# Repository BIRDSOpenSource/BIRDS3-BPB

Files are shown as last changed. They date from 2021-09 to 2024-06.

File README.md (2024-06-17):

<p align="center">
<a href="https://lean-sat.org/opensource/" class="button icon calendar">Join Monthly Webinar</a>
</p>

<div align="center">

</div>

# BIRDS3-BPB
The two different designs of the BPB used in the BIRDS3 mission, one with CPLD and one without.

## About the BIRDS3 Program:



The project was led by Kyushu Institute of Technology in Japan and involves students from Sri Lanka, Bhutan, Nepal and Japan.
Satellite Names: NepaliSat-1 (Nepal), Raavana-1 (Sri Lanka) and Ugiusu (Japan)

Stakeholders: Nepal Academy of Science and Technology (NAST) for Nepal, Arthur C Clarke Institute for Modern Technologies (ACCIMT) for Sri Lanka, and Kyushu Institute of Technology (Kyutech) for Japan.

Project duration: 2018-2020

CubeSat: 1U (10x10x10) cm3

Weight: 1.13kg

Launch Date: 17th April 2019

BIRDS-3 has 4 main missions in total; LoRa Demonstration Mission (LDM), Imaging Mission (CAM), Attitude Determination and Control Mission (ADCS) and Software Configurable Backplane Mission (BPB) 

## Organisation structure

## Features

## I like this project, can I help you?
You are welcome 🙂

* Give us a star ⭐
* Watch repository to be notified about updates 👀
* If you will find some errors, report them in Issues 🐞
* Try Birds designs on some real computer and let us know how it worked in Discussions. 💬
* We would greatly appreciate if you would also tell others about this ecosystem, it helps us to improve BIRDS Open Source. Thank you!

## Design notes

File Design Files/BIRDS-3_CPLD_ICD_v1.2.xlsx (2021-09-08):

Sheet: Version
BIRDS-3 BPB/CPLD Revision History
Date | Version | Person | Revision
22.05.18 | 1.0 | Abhas | Initial release of BPB/CPLD, updated with Turo

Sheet: Pin Assignment
 |  |  |  |  |  |  |  |  |  | `
C101 connector on the back plane |  | C102 connector on the back plane |  |  | C103 connector on the back plane |  | C104 connector on the back plane |  |  | C105 connector on the back plane |  |  | C106 connector on the back plane
FAB, Front access |  | EPS&OBC |  |  | COM |  | LDM |  |  | MSN II, Mission |  |  | RAB, Rear access
1 | Programming/debug 1 (DEV1 PGC) | 1 | Programming/debug 1 (DEV1 PGC) |  | 1 | COM_to_RAB GIO1 (DATA PROG PIN 1) | 1 | COM_to_RAB GIO1 (DATA PROG PIN 1) |  | 1 | COM_to_RAB GIO1 (DATA PROG PIN 1) |  | 1 | COM_to_RAB GIO1 (DATA PROG PIN 1)
2 | Programming/debug 2 (DEV 2 PGD) | 2 | Programming/debug 2 (DEV 2 PGD) |  | 2 | COM_to_RAB GIO2 (DATA PROG PIN 2) | 2 | COM_to_RAB GIO2 (DATA PROG PIN 2) |  | 2 | COM_to_RAB GIO2 (DATA PROG PIN 2) |  | 2 | COM_to_RAB GIO2 (DATA PROG PIN 2)
3 | Programming/debug 3 (DEV3 MCLR_FP) | 3 | Programming/debug 3 (DEV3 MCLR_FP) |  | 3 | COM_to_RAB GIO3 (DATA PROG PIN 3) | 3 | COM_to_RAB GIO3 (DATA PROG PIN 3) |  | 3 | COM_to_RAB GIO3 (DATA PROG PIN 3) |  | 3 | COM_to_RAB GIO3 (DATA PROG PIN 3)
4 | Programming/debug 4 (DEV4 MCLR_RP) | 4 | Programming/debug 4 (DEV4 MCLR_RP) |  | 4 | COM_to_RAB GIO4 (ADCS PROG PIN 1) | 4 | COM_to_RAB GIO4 (ADCS PROG PIN 1) |  | 4 | COM_to_RAB GIO4 (ADCS PROG PIN 1) |  | 4 | COM_to_RAB GIO4 (ADCS PROG PIN 1)
5 | Programming/debug 5 (DEV5 MCLR_CP) | 5 | Programming/debug 5 (DEV5 MCLR_CP) |  | 5 | COM_to_RAB GIO5 | 5 | COM_to_RAB GIO5 |  | 5 | MTQ_PWR_-X |  | 5 | MTQ_PWR_-X
6 | Programming/debug 6 (DEV6 MCLR_MP) | 6 | Programming/debug 6 (DEV6 MCLR_MP) |  | 6 | COM_to_RAB GIO6 | 6 | COM_to_RAB GIO6 |  | 6 | MTQ_RTN_-X |  | 6 | MTQ_RTN_-X
7 | FAB_to_RAB GIO 1 (ADCS PROG PIN 2) | 7 | OBC-COM 1 |  | 7 | OBC-COM 1 | 7 | FAB_to_RAB GIO 1 (ADCS PROG PIN 2) |  | 7 | FAB_to_RAB GIO 1 (ADCS PROG PIN 2) |  | 7 | FAB_to_RAB GIO 1 (ADCS PROG PIN 2)
8 | FAB_to_RAB GIO 2 (ADCS PROG PIN 3) | 8 | OBC-COM 2 |  | 8 | OBC-COM 2 | 8 | FAB_to_RAB GIO 2 (ADCS PROG PIN 3) |  | 8 | FAB_to_RAB GIO 2 (ADCS PROG PIN 3) |  | 8 | FAB_to_RAB GIO 2 (ADCS PROG PIN 3)
9 | FAB_to_RAB GIO 3(BC TEMP IN) | 9 | FAB_to_RAB GIO 3(BC TEMP IN) |  | 9 | FAB_to_RAB GIO 3(BC TEMP IN) | 9 | FAB_to_RAB GIO 3(BC TEMP IN) |  | 9 | FAB_to_RAB GIO 3(BC TEMP IN) |  | 9 | FAB_to_RAB GIO 3(BC TEMP IN)
10 | FAB_to_RAB GIO 4(MAIN_PIC_DIO to RAB BC) | 10 | FAB_to_RAB GIO 4(MAIN_PIC_DIO to RAB BC) |  | 10 | FAB_to_RAB GIO 4(MAIN_PIC_DIO to RAB BC) | 10 | FAB_to_RAB GIO 4(MAIN_PIC_DIO to RAB BC) |  | 10 | FAB_to_RAB GIO 4(MAIN_PIC_DIO to RAB BC) |  | 10 | FAB_to_RAB GIO 4(MAIN_PIC_DIO to RAB BC)
11 | FAB_to_RAB GIO 5(MAIN_PIC_DIO to ADCS) | 11 | FAB_to_RAB GIO 5(MAIN_PIC_DIO to ADCS) |  | 11 | FAB_to_RAB GIO 5(MAIN_PIC_DIO to ADCS) | 11 | FAB_to_RAB GIO 5(MAIN_PIC_DIO to ADCS) |  | 11 | FAB_to_RAB GIO 5(MAIN_PIC_DIO to ADCS) |  | 11 | FAB_to_RAB GIO 5(MAIN_PIC_DIO to ADCS)
12 | FAB_to_RAB GIO 6 (MAIN_PIC_DIO to CAM) | 12 | FAB_to_RAB GIO 6 (MAIN_PIC_DIO to CAM) |  | 12 | FAB_to_RAB GIO 6 (MAIN_PIC_DIO to CAM) | 12 | FAB_to_RAB GIO 6 (MAIN_PIC_DIO to CAM) |  | 12 | FAB_to_RAB GIO 6 (MAIN_PIC_DIO to CAM) |  | 12 | FAB_to_RAB GIO 6 (MAIN_PIC_DIO to CAM)
13 | GND_SYS | 13 | GND_SYS |  | 13 | GND_SYS | 13 | GND_SYS |  | 13 | GND_SYS |  | 13 | GND_SYS
14 | GND_SYS | 14 | GND_SYS |  | 14 | GND_SYS | 14 | GND_SYS |  | 14 | GND_SYS |  | 14 | GND_SYS
15 | SUP_5V0 | 15 | SUP_5V0 |  | 15 | SUP_5V0 | 15 | SUP_5V0 |  | 15 | SUP_5V0 |  | 15 | SUP_5V0
16 | SUP_5V0 | 16 | SUP_5V0 |  | 16 | SUP_5V0 | 16 | SUP_5V0 |  | 16 | SUP_5V0 |  | 16 | SUP_5V0
17 | FAB_to_OBC GIO 1 (MPIC_UART_TX_EXT) | 17 | FAB_to_OBC GIO 1 (MPIC_UART_TX_EXT) |  | 17 | CPLD-PIN 19 | 17 | CPLD-PIN 39 (MAIN_PIC_UART_TX to DATA) | INPUT TO MSN | 17 | MTQ_PWR_-Z |  | 17 | CPLD-PIN 65
18 | FAB_to_OBC GIO 2 (MPIC_UART_RX_EXT) | 18 | FAB_to_OBC GIO 2 (MPIC_UART_RX_EXT) |  | 18 | CPLD-PIN 20 | 18 | CPLD-PIN 40 (MAIN_PIC_UART_RX to DATA) | OUTPUT FROM MSN | 18 | MTQ_RTN_-Z |  | 18 | CPLD-PIN 66
19 | FAB_to_OBC GIO 3 (MPIC_FAB_UART_TX) | 19 | FAB_to_OBC GIO 3 (MPIC_FAB_UART_TX) |  | 19 | CPLD-PIN 21 | 19 | CPLD-PIN 41 (MAIN_PIC_DIO to DATA) | INPUT TO MSN | 19 | MTQ_PWR_-Y |  | 19 | CPLD-PIN 67
20 | FAB_to_OBC GIO 4 (MPIC_FAB_UART_RX) | 20 | FAB_to_OBC GIO 4 (MPIC_FAB_UART_RX) |  | 20 | CPLD-PIN 22 | 20 | CPLD-PIN 42 |  | 20 | MTQ_RTN_-Y |  | 20 | CPLD-PIN 68
21 | POWERSC_-Y | 21 | CPLD-PIN 8 (MAIN_PIC_UART_TX to DATA) | OUTPUT FROM OBC | 21 | CPLD-PIN 23 | 21 | CPLD-PIN 43 |  | 21 | CPLD-PIN XX (not decided) |  | 21 | CPLD-PIN 69
22 | TEMP_2 (-Y panel) | 22 | CPLD-PIN 9 (MAIN_PIC_UART_RX to DATA) | INPUT TO OBC | 22 | CPLD-PIN 24 | 22 | CPLD-PIN 44 |  | 22 | CPLD-PIN XX (not decided) |  | 22 | CPLD-PIN 70 |  | CN303 Battery Connector is not directly connected to Backplane, Connected to FAB
23 | SUP_UNREG_1 | 23 | SUP_UNREG_1 |  | 23 | SUP_UNREG_1 | 23 | SUP_UNREG_1 |  | 23 | SUP_UNREG_1 |  | 23 | SUP_UNREG_1
24 | SUP_UNREG_1 | 24 | SUP_UNREG_1 |  | 24 | SUP_UNREG_1 | 24 | SUP_UNREG_1 |  | 24 | SUP_UNREG_1 |  | 24 | SUP_UNREG_1
25 | SUP_3V3_2 | 25 | SUP_3V3_2 |  | 25 | SUP_3V3_2 | 25 | SUP_3V3_2 |  | 25 | SUP_3V3_2 |  | 25 | SUP_3V3_2 |  | Battery
26 | SUP_3V3_2 | 26 | SUP_3V3_2 |  | 26 | SUP_3V3_2 | 26 | SUP_3V3_2 |  | 26 | SUP_3V3_2 |  | 26 | SUP_3V3_2 |  | 1 | GND_ROOT
27 | POWERSC_+X | 27 | CPLD-PIN 10 (MAIN_PIC_UART_TX To CAM) | OUTPUT FROM OBC | 27 | CPLD-PIN 25 | 27 | CPLD-PIN 45 (MAIN_PIC_UART_TX To CAM) | INPUT TO MSN | 27 | CPLD-PIN 45 (MAIN_PIC_UART_TX To CAM) | INPUT TO MSN | 27 | CPLD-PIN 71 |  | 2 | GND_ROOT
28 | TEMP_1 (+X) | 28 | CPLD-PIN 11 (MAIN_PIC_UART_RX To CAM) | INPUT TO OBC | 28 | CPLD-PIN 26 | 28 | CPLD-PIN 46 (MAIN_PIC_UART_RX To CAM) | OUTPUT FROM MSN | 28 | CPLD-PIN 46 (MAIN_PIC_UART_RX To CAM) | OUTPUT FROM MSN | 28 | CPLD-PIN 72 |  | 3 | GND_ROOT
29 | RAW_POWER | 29 | RAW_POWER |  | 29 | CPLD-PIN 27 | 29 | CPLD-PIN 47 |  | 29 | CPLD-PIN 47 |  | 29 | CPLD-PIN 73 |  | 4 | GND_ROOT
30 | RAW_POWER | 30 | RAW_POWER |  | 30 | CPLD-PIN 28 | 30 | CPLD-PIN 48 |  | 30 | CPLD-PIN 48 |  | 30 | CPLD-PIN 74 |  | 5 | N.C.
31 | POWERSC_-X | 31 | CPLD-PIN 12 (FM2_SPI_CS) | INPUT TO OBC | 31 | CPLD-PIN 29 | 31 | CPLD-PIN 49 (FM2_SPI_CS) | OUTPUT FROM MSN | 31 | CPLD-PIN 49 (FM2_SPI_CS) | OUTPUT FROM MSN | 31 | CPLD-PIN 75 |  | 6 | PWR_BAT
32 | TEMP_5 (-X panel) | 32 | CPLD-PIN 13 (FM2_SPI_MOSI) | INPUT TO OBC | 32 | CPLD-PIN 30 | 32 | CPLD-PIN 50 (FM2_SPI_MOSI) | OUTPUT FROM MSN | 32 | CPLD-PIN 50 (FM2_SPI_MOSI) | OUTPUT FROM MSN | 32 | CPLD-PIN 76 |  | 7 | PWR_BAT
33 | POWERSC_-Z | 33 | CPLD-PIN 14 (FM2_SPI_MISO) | OUTPUT FROM OBC | 33 | CPLD-PIN 31 | 33 | CPLD-PIN 51 (FM2_SPI_MISO) | INPUT TO MSN | 33 | CPLD-PIN 51 (FM2_SPI_MISO) | INPUT TO MSN | 33 | CPLD-PIN 77 |  | 8 | PWR_BAT
34 | TEMP_3 (-Z panel) | 34 | CPLD-PIN 15 (FM2_SPI_SCK) | INPUT TO OBC | 34 | CPLD-PIN 32 | 34 | CPLD-PIN 52 (FM2_SPI_SCK) | OUTPUT FROM MSN | 34 | CPLD-PIN 52 (FM2_SPI_SCK) | OUTPUT FROM MSN | 34 | CPLD-PIN 78 |  | 9 | PWR_BAT
35 | SUP_UNREG_2 | 35 | SUP_UNREG_2 |  | 35 | SUP_UNREG_2 | 35 | SUP_UNREG_2 |  | 35 | SUP_UNREG_2 |  | 35 | SUP_UNREG_2 |  | 10 | HEATER_CNTRL_BAT
36 | SUP_UNREG_2 | 36 | SUP_UNREG_2 |  | 36 | SUP_UNREG_2 | 36 | SUP_UNREG_2 |  | 36 | SUP_UNREG_2 |  | 36 | SUP_UNREG_2 |  | 11 | TEMP_SENSOR_1
37 | POWERSC_+Y | 37 | CPLD-PIN 16 (MAIN_PIC_UART_TX To ADCS) | OUTPUT FROM OBC | 37 | CPLD-PIN 33 | 37 | CPLD-PIN 53 (CAM_UART_TX0) | OUTPUT FROM MSN | 37 | CPLD-PIN 53 (CAM_UART_TX0) | OUTPUT FROM MSN | 37 | CPLD-PIN 79 (CAM_UART_TX0) | INPUT TO RAB | 12 | TEMP_SENSOR_2
38 | TEMP_4 (+Y panel) | 38 | CPLD-PIN 17 (MAIN_PIC_UART_RX To ADCS) | INPUT TO OBC | 38 | CPLD-PIN 34 | 38 | CPLD-PIN 54 (CAM_UART_RX0) | INPUT TO MSN | 38 | CPLD-PIN 54 (CAM_UART_RX0) | INPUT TO MSN | 38 | CPLD-PIN 80 (CAM_UART_RX0) | OUTPUT FROM RAB
39 | Kill SW | 39 | Kill SW |  | 39 | CPLD-PIN 35 | 39 | CPLD-PIN 55 (CAM_DTR) | INPUT TO MSN | 39 | CPLD-PIN 55 (CAM_DTR) | INPUT TO MSN | 39 | CPLD-PIN 81 (CAM_DTR) | OUTPUT FROM RAB
40 | DEP_SW-1 | 40 | DEP_SW-1 |  | 40 | CPLD-PIN 36 | 40 | CPLD-PIN 56 |  | 40 | CPLD-PIN 56 |  | 40 | CPLD-PIN 82
41 | DEP_SW-2 | 41 | DEP_SW-2 |  | 41 | CPLD-PIN 37 | 41 | CPLD-PIN 57 |  | 41 | CPLD-PIN 57 |  | 41 | CPLD-PIN 83
42 | CPLD-PIN 1 / DEP_SW-3 | 42 | CPLD-PIN 18 (MAIN_PIC_DIO to Data) | OUTPUT FROM OBC | 42 | CPLD-PIN 38 | 42 | CPLD-PIN 58 |  | 42 | CPLD-PIN 58 |  | 42 | CPLD-PIN 84
43 | CPLD-PIN 2 / DEP_SW-4 | 43 | OBC-COM 3 |  | 43 | OBC-COM 3 | 43 | CPLD-PIN 59 (MAIN_PIC_UART_TX To ADCS) | INPUT TO MSN | 43 | CPLD-PIN 59 (MAIN_PIC_UART_TX To ADCS) | INPUT TO MSN | 43 | CPLD-PIN 85
44 | CPLD-PIN 3 / TEMP_6 | 44 | OBC-COM 4 |  | 44 | OBC-COM 4 | 44 | CPLD-PIN 60 (MAIN_PIC_UART_RX To ADCS) | OUTPUT FROM MSN | 44 | CPLD-PIN 60 (MAIN_PIC_UART_RX To ADCS) | OUTPUT FROM MSN | 44 | CPLD-PIN 86
45 | CPLD-PIN 4 | 45 | OBC-COM 5 |  | 45 | OBC-COM 5 | 45 | CPLD-PIN 61 |  | 45 | CPLD-PIN 61 |  | 45 | CPLD-PIN 87
46 | CPLD-PIN 5 | 46 | OBC-COM 6 |  | 46 | OBC-COM 6 | 46 | CPLD-PIN 62 |  | 46 | CPLD-PIN 62 |  | 46 | CPLD-PIN 88
47 | CPLD-PIN 6 | 47 | OBC-COM 7 |  | 47 | OBC-COM 7 | 47 | CPLD-PIN 63 |  | 47 | CPLD-PIN 63 |  | 47 | CPLD-PIN 89
48 | CPLD-PIN 7 | 48 | OBC-COM 8 |  | 48 | OBC-COM 8 | 48 | CPLD-PIN 64 |  | 48 | CPLD-PIN 64 |  | 48 | CPLD-PIN 90
49 | SUP_3V3_1 | 49 | SUP_3V3_1 |  | 49 | SUP_3V3_1 | 49 | SUP_3V3_1 |  | 49 | SUP_3V3_1 |  | 49 | SUP_3V3_1
50 | SUP_3V3_1 | 50 | SUP_3V3_1 |  | 50 | SUP_3V3_1 | 50 | SUP_3V3_1 |  | 50 | SUP_3V3_1 |  | 50 | SUP_3V3_1
*Same colours and names are representing the same connection

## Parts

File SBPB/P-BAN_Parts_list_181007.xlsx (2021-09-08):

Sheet: 必ずお読みください
入力項目説明
メ ー カ ー |  |  | 電子部品のメーカー名をご入力ください。
部 品 種 別 |  |  | 電子部品の種別をご入力ください。例：チップ抵抗、トランジスタ、LED、など
電 子 部 品 型 番 |  |  | 電子部品の型番をご入力ください。 ※誤表記による不具合を回避するためにも正確なご入力をお願い致します。 ※表面実装の抵抗やコンデンサ(電解、タンタル以外)は、後述「電子部品見取り表」をご参照のうえ、ご入力ください。
配 置 記 号 / リファレンス |  |  | シルク図/配置図に表記された配置記号/リファレンス番号をご入力ください。 ※複数入力する場合は、カンマ「,」区切りでのご入力をお願い致します。 ※電子部品型番ベースでのご記入をお願い致します。（１つの電子部品型番に対して、配置番号を複数記入）
個 数 |  |  | 電子部品の個数をご入力ください。
ピ ン 数 |  |  | 電子部品の総ピン数をご入力ください。 ※基板取付穴、部品取付穴、全てのスルー・ノンスルーホール、面実装部品のパッド、及び次の①～⑤の配線を伴う箇所（①テストピン、②チェックランド、③引き出しランド、④ジャンパピン、⑤入出力ランドの総計。
実装 / 未実装 |  |  | 実装サービスでの「実装」/「未実装」をご選択ください。 ※同じ電子部品型番の中で実装と未実装が分かれる場合は、それぞれ2行に分けて配置記号をご入力ください。
部品分類 | SMD |  | 表面実装部品
 | DIP |  | 挿入部品
 | 特殊 BGA等 |  | BGA/CSP/LGA/QFNなど部品極性が部品の真下に配置された部品 -BGA：Ball Grid Array/下面に半田ボールの端子を配置したパッケージ。 -CSP：Chip Size Package/チッププサイズと同じか、もしくは僅かに大きいパッケージ。 -LGA：Land Grid Array/裏面に外部入出力用のランドを設けたパッケージ。※BGAの半田ボールがない。 -QFN：Quad Flat Non-Lead Package/QFPに似ていますが、外部入出力用のピンが出ていないパッケージ。
P板.com提供部品 (無料) |  |  | 【無償提供部品一覧】シートに記載されている「メーカー型番」を【部品リスト入力フォーム】シートのD列（電子部品型番）に入力し、I列（実装／未実装）を「実装」に設定いただくと、自動的に「○」が表示されます。 ※無料提供部品：チップコンデンサ/チップ抵抗を約1000種、実装サービスをご利用のお客様に無料提供いたします。 ※「○」が付かない場合は全半角の不一致などにより誤判定されている可能性があります。【無償提供部品一覧】シートより型番をコピー＆ペーストにて【部品リスト入力フォーム】にご入力ください。
 |  |  | http://www.p-ban.com/implementation/chip.html
P板.com調達部品(有料） |  |  | P板.com実装サービスで部品調達を希望される場合に○をご選択ください。 ※調達費用のお見積もりは、部品リストの返却と同時にご連絡いたします。 ※ご希望の納期や市場在庫状況によっては、調達が不可となる部品もございますので、予めご了承ください。
パッケージ情報 部品外形/部品仕様 |  |  | 電子部品のパッケージ情報をご入力ください。例：1608 , DIP , 0.5mmピッチQFP , 0.4mmピッチCN
コ メ ン ト |  |  | 特別なご指示のある電子部品について、自由にご入力ください。 例：未実装挿入穴のマスク処理が必要、など
版、変更履歴 |  |  | 部品種毎に、変更履歴を記載してください。 版は、アカウント登録の版に合わせて記載ください。
調達型式、代替型式 |  |  | 無料提供部品の在庫切れや、正確な調達型式を記載いたします。
部品名称見取り表
1.チップ部品（抵抗、コンデンサ）
 |  |  |  |  | 単位：ｍｍ
 |  |  | 電子部品型番 (C:コンデンサ、R:抵抗） | Ａ寸法 | Ｂ寸法
 |  |  | C/R1608 | 1.6 | 0.8
 |  |  | C/R2125 | 2 | 1.25
 |  |  | C/R3216 | 3.2 | 1.6
 |  |  | C/R3225 | 3.2 | 2.5
 |  |  | C/R4532 | 4.5 | 3.2
2.チップタンタルコンデンサ
 |  |  |  |  | 単位：ｍｍ
 |  |  | 電子部品型番 | Ａ寸法 | Ｂ寸法
 |  |  | CT3216 | 3.2 | 1.6
 |  |  | CT3528 | 3.5 | 2.8
 |  |  | CT4726 | 4.7 | 2.6
 |  |  | CT6032 | 6 | 3.2
 |  |  | CT5846 | 5.8 | 4.6
 |  |  | CT7343 | 7.3 | 4.3
3.チップアルミ電解コンデンサ
 |  |  |  |  |  | 単位：ｍｍ
 |  |  | 電子部品型番 | Ａ寸法 | Ｂ寸法 | C寸法
 |  |  | CE33 | 3.3 | 3.3 | φ3.0
 |  |  | CE43 | 4.3 | 4.3 | φ4.0
 |  |  | CE53 | 5.3 | 5.3 | φ5.0
 |  |  | CE66 | 6.6 | 6.6 | φ6.3
 |  |  | CE83 | 8.3 | 8.3 | φ8.0
 |  |  | CE103 | 10.3 | 10.3 | φ10.0
部品取り付け穴は、ピン数に含めてください。
コネクタの場合 |  |  |  |  |  | トランスの場合
部品リストフォーマット変更履歴
2014-02-01 | v2.0 | 松森 | 部品種別の総計を、直接関数に変更
 |  |  | ピン数合計、実装数合計数量を、直接関数に変更
 |  |  | 部品調達見積欄を修正
2014-03-11 | v2.1 | 松森 | *N列、O列が下の方、"○"選択リスト消えていたのを追加
 |  |  | *縮小しても解像度崩れず文字表示するため、フォントを"Meiryo UI"(Windows 標準添付)に変更
 |  |  | *136行目以降を非表示
 |  |  | *"X"列にリストを埋め込み
2014-06-12 | v2.2 | 松森 | *固定行を変更
 |  |  | *在庫状況列に条件付き書式設定
 |  |  | *その他各種バグ修正
2015-03-31 | V2.3 | 松森 | *無償提供部品を記載すると、無償提供部品欄に自動で"○"が表示されるよう条件式を挿入
 |  |  | *併せて、無償提供部品参照用一覧シートの作成・追加
 |  |  | *最小購入数が必要数量を下回る場合、セルを赤色にハッチングする
 |  |  | *シート1の名称変更
 |  |  | *変更履歴シートの追加
2015-06-19 | v2.4 | 松森 | ・ゼロΩ抵抗を無償対象に追加
 |  |  | ・変更履歴の列を追加し、変更履歴シートを削除
 |  |  | ・その他書式、印刷機能の変更
 |  |  | ・無償提供部品の入れ替え
2015-08-14 | v2.5 | 松森 | ・ゼロΩ抵抗の無償対象品が正しく反映されていなかったバグ修正
 |  |  | ・フォームへバージョン情報を埋め込み
2015-11-05 | v2.6 | 上田 | ・無償提供部品(RK73H2ATTD1601F)の抵抗値を正しい値に修正
2015-11-09 | v2.7 | 上田 | ・P板.com調達部品(無料)欄のフォントを変更
2016-01-15 | v2.8 | 箕浦 | ・無償提供部品一覧の「GRM32NF11E106Z」を削除
 |  |  | ・部品リスト入力フォームの4行目F列～L列の計算式が136行目以降を対象としていなかった不具合を修正
2016-01-27 | v2.9 | 箕浦 | ・「無償提供部品一覧」シートの表記修正

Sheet: 部品リスト入力フォーム
Ver.8.0 |  |  | 電 子 部 品 型 番 ※半角英数字 ※サフィックスまで入力必須 | 配 置 記 号 リ フ ァ レ ン ス ※半角英数字） | 個数 | ピ ン 数 (部品取付穴 を含む） |  | 実装/ 未実装 | 部 品 分 類 |  |  | 必要数 実装枚数を入れてください。 ↓ | P板.com 提供 部品 (無料) | P板.com 調達 部品 (有料） | パッケージ情報 部品外形/部品仕様 | コ メ ン ト ※未実装挿入穴の マスク処理が必要、など | 版 変更履歴 | 入荷数 | 返却
No | メーカー | 部品種別 |  |  |  | 1個 あたり | 合計 | 実装個数 | SMD | DIP | 特殊 BGA等 |  |  |  |  |  |  |  |  | 部品調達使用欄
 |  |  |  |  | 28 | 246 | #VALUE! | 28 | 18 | 10 | 0 | 2 | リスト (http://www.p-ban.com/implementation/chip.html)
例 | KOA | チップ抵抗 | RK73B2ATTD1002F | R1,R5,R9,R10 | 4 | 2 | 8 | 未実装 | SMD |  |  |  |  |  | 2012 |  | 4版 型式訂正、個数変更、 実装→未実装へ |  |  | 必要数 | 調達数 | 在庫状況 | 納期
Eg. | Manufacturer | Description | Device | Part no. | Qty. | No. of legs | #VALUE! |  |  |  |  |  |  |  | Package | Remarks |  |  | □
 |  |  |  |  |  |  |  |  |  |  |  |  |  |  |  |  |  |  | □
1 | Lattice | lattice ispmach4000ze CPLD | LC4256ZE_XXTN144 | IC2 | 1 | 144 | 144 | 実装 | SMD |  |  | 2 |  |  | TQFP144 |  |  |  | □
2 | MURATA | CAPACITOR | GRM21BB30J226M | C1 | 1 | 2 | 2 | 実装 | SMD |  |  | 2 |  |  | 2012 | 22uF |  |  | □
3 | MURATA | CAPACITOR | GRM21BB31E475K | C2 | 1 | 2 | 2 | 実装 | SMD |  |  | 2 |  |  | 2012 | 4.7uF |  |  | □
4 | MURATA | CAPACITOR | GRM155B11A104K | C3,C4,C5,C7 | 4 | 2 | 8 | 実装 | SMD |  |  | 8 | O |  | 1005 | 0.1uF
5 | KOA | RESISTOR | RK73H1ETTP5601F | R1, R2, R3, R4 | 4 | 2 | 8 | 実装 | SMD |  |  | 8 | O |  | 1005 | 5.60k |  |  | □
6 | KOA | RESISTOR | RK73Z2BTTD | R6, R8 | 2 | 2 | 4 | 実装 | SMD |  |  | 4 | O |  | 3216 | 0 |  |  | □
7 | MURATA | FERRITE BEAD 600 OHM 0603 1LN | BLM18AG601SN1D | L1 | 1 | 2 | 2 | 実装 | SMD |  |  | 2 |  |  | 1608 | 600 Ohm @ 100MHz |  |  | □
8 | ON Semiconductor | REG LINEAR 1.8V 1A | NCV1117ST18T3G | DC1V8 | 1 | 4 | 4 | 実装 | SMD |  |  | 2 |  |  | SOT223 |  |  |  | □
9 | HIROSUGI | CONNECTOR | PSR-210154-12 | SP1, SP3, SP4 | 3 | 12 | 36 | 実装 | DIP |  |  | 6 |  |  | 1x12 pin header | 2mm pitch, 12 pin, right angle |  |  | □
10 | HIROSUGI | CONNECTOR | PSS-210204-12 | SP5 | 1 | 12 | 12 | 実装 | DIP |  |  | 2 |  |  | 1x12 pin header | 2mm pitch, 12 pin |  |  | □
11 | Analog Devices Inc. | SENSOR TEMPERATURE | TMP36FSZ | T1 | 1 | 8 | 8 | 実装 | SMD |  |  | 2 |  |  | 8-SOIC
12 | HIROSE | CONNECTOR | A3C-50DA-2DSA(71) | C101, C102, C103, C104, C105, C106 | 6 | 50 | 300 | 実装 | DIP |  |  | 12 |  |  | 2x25 header | 2mm pitch, 50 pin
13 | MOLEX | CONNECTOR | 554600272 | SW1, SW2 | 2 | 4 | 8 | 実装 | SMD |  |  | 4 |  |  | 2 pin, Shrouded | Connector Header Surface Mount 2mm
14
15
16
17
18
19
20
21
22
23
24
25
26
27
28
29
30
31
32
33
34
35
36
37
38
39
40
41
42
43
44
45
46
 |  |  |  |  |  |  |  |  |  |  |  |  |  |  |  |  |  |  | □
 |  |  |  |  |  |  |  |  |  |  |  |  |  |  |  |  |  |  | □
 |  |  |  |  |  |  |  |  |  |  |  |  |  |  |  |  |  |  | □
 |  |  |  |  |  |  |  |  |  |  |  |  |  |  |  |  |  |  | □
 |  |  |  |  |  |  |  |  |  |  |  |  |  |  |  |  |  |  | □
 |  |  |  |  |  |  |  |  |  |  |  |  |  |  |  |  |  |  | □
 |  |  |  |  |  |  |  |  |  |  |  |  |  |  |  |  |  |  | □
 |  |  |  |  |  |  |  |  |  |  |  |  |  |  |  |  |  |  | □
 |  |  |  |  |  |  |  |  |  |  |  |  |  |  |  |  |  |  | □
 |  |  |  |  |  |  |  |  |  |  |  |  |  |  |  |  |  |  | □
 |  |  |  |  |  |  |  |  |  |  |  |  |  |  |  |  |  |  | □
 |  |  |  |  |  |  |  |  |  |  |  |  |  |  |  |  |  |  | □
 |  |  |  |  |  |  |  |  |  |  |  |  |  |  |  |  |  |  | □
 |  |  |  |  |  |  |  |  |  |  |  |  |  |  |  |  |  |  | □
 |  |  |  |  |  |  |  |  |  |  |  |  |  |  |  |  |  |  | □
 |  |  |  |  |  |  |  |  |  |  |  |  |  |  |  |  |  |  | □
 |  |  |  |  |  |  |  |  |  |  |  |  |  |  |  |  |  |  | □
 |  |  |  |  |  |  |  |  |  |  |  |  |  |  |  |  |  |  | □
 |  |  |  |  |  |  |  |  |  |  |  |  |  |  |  |  |  |  | □
 |  |  |  |  |  |  |  |  |  |  |  |  |  |  |  |  |  |  | □
 |  |  |  |  |  |  |  |  |  |  |  |  |  |  |  |  |  |  | □
 |  |  |  |  |  |  |  |  |  |  |  |  |  |  |  |  |  |  | □
 |  |  |  |  |  |  |  |  |  |  |  |  |  |  |  |  |  |  | □
 |  |  |  |  |  |  |  |  |  |  |  |  |  |  |  |  |  |  | □
 |  |  |  |  |  |  |  |  |  |  |  |  |  |  |  |  |  |  | □
 |  |  |  |  |  |  |  |  |  |  |  |  |  |  |  |  |  |  | □
 |  |  |  |  |  |  |  |  |  |  |  |  |  |  |  |  |  |  | □
 |  |  |  |  |  |  |  |  |  |  |  |  |  |  |  |  |  |  | □
 |  |  |  |  |  |  |  |  |  |  |  |  |  |  |  |  |  |  | □
 |  |  |  |  |  |  |  |  |  |  |  |  |  |  |  |  |  |  | □
 |  |  |  |  |  |  |  |  |  |  |  |  |  |  |  |  |  |  | □
 |  |  |  |  |  |  |  |  |  |  |  |  |  |  |  |  |  |  | □
 |  |  |  |  |  |  |  |  |  |  |  |  |  |  |  |  |  |  | □
 |  |  |  |  |  |  |  |  |  |  |  |  |  |  |  |  |  |  | □
 |  |  |  |  |  |  |  |  |  |  |  |  |  |  |  |  |  |  | □
 |  |  |  |  |  |  |  |  |  |  |  |  |  |  |  |  |  |  | □
 |  |  |  |  |  |  |  |  |  |  |  |  |  |  |  |  |  |  | □
 |  |  |  |  |  |  |  |  |  |  |  |  |  |  |  |  |  |  | □
 |  |  |  |  |  |  |  |  |  |  |  |  |  |  |  |  |  |  | □
 |  |  |  |  |  |  |  |  |  |  |  |  |  |  |  |  |  |  | □
 |  |  |  |  |  |  |  |  |  |  |  |  |  |  |  |  |  |  | □
 |  |  |  |  |  |  |  |  |  |  |  |  |  |  |  |  |  |  | □
 |  |  |  |  |  |  |  |  |  |  |  |  |  |  |  |  |  |  | □
 |  |  |  |  |  |  |  |  |  |  |  |  |  |  |  |  |  |  | □
 |  |  |  |  |  |  |  |  |  |  |  |  |  |  |  |  |  |  | □
 |  |  |  |  |  |  |  |  |  |  |  |  |  |  |  |  |  |  | □
 |  |  |  |  |  |  |  |  |  |  |  |  |  |  |  |  |  |  | □

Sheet: 無償提供部品一覧
このシートの内容は変更しないでください。
メーカー型番 |  | メーカー | サイズ | 定数 | 許容差 | 定格
RK73Z1ETTP | ○ | KOA | 1005 | 0 |  | 1A
RK73H1ETTP1R00F | ○ | KOA | 1005 | 1 | ±1% | 0.063W
RK73B1ETTP1R0J | ○ | KOA | 1005 | 1 | ±5% | 0.063W
RK73H1ETTP1R10F | ○ | KOA | 1005 | 1.1 | ±1% | 0.063W
RK73B1ETTP1R1J | ○ | KOA | 1005 | 1.1 | ±5% | 0.063W
RK73H1ETTP1R20F | ○ | KOA | 1005 | 1.2 | ±1% | 0.063W
RK73B1ETTP1R2J | ○ | KOA | 1005 | 1.2 | ±5% | 0.063W
RK73H1ETTP1R30F | ○ | KOA | 1005 | 1.3 | ±1% | 0.063W
RK73B1ETTP1R3J | ○ | KOA | 1005 | 1.3 | ±5% | 0.063W
RK73H1ETTP1R50F | ○ | KOA | 1005 | 1.5 | ±1% | 0.063W
RK73B1ETTP1R5J | ○ | KOA | 1005 | 1.5 | ±5% | 0.063W
RK73H1ETTP1R60F | ○ | KOA | 1005 | 1.6 | ±1% | 0.063W
RK73B1ETTP1R6J | ○ | KOA | 1005 | 1.6 | ±5% | 0.063W
RK73H1ETTP1R80F | ○ | KOA | 1005 | 1.8 | ±1% | 0.063W
RK73B1ETTP1R8J | ○ | KOA | 1005 | 1.8 | ±5% | 0.063W
RK73H1ETTP2R00F | ○ | KOA | 1005 | 2 | ±1% | 0.063W
RK73B1ETTP2R0J | ○ | KOA | 1005 | 2 | ±5% | 0.063W
RK73H1ETTP2R20F | ○ | KOA | 1005 | 2.2 | ±1% | 0.063W
RK73B1ETTP2R2J | ○ | KOA | 1005 | 2.2 | ±5% | 0.063W
RK73H1ETTP2R40F | ○ | KOA | 1005 | 2.4 | ±1% | 0.063W
RK73B1ETTP2R4J | ○ | KOA | 1005 | 2.4 | ±5% | 0.063W
RK73H1ETTP2R70F | ○ | KOA | 1005 | 2.7 | ±1% | 0.063W
RK73B1ETTP2R7J | ○ | KOA | 1005 | 2.7 | ±5% | 0.063W
RK73H1ETTP3R00F | ○ | KOA | 1005 | 3 | ±1% | 0.063W
RK73B1ETTP3R0J | ○ | KOA | 1005 | 3 | ±5% | 0.063W
RK73H1ETTP3R30F | ○ | KOA | 1005 | 3.3 | ±1% | 0.063W
RK73B1ETTP3R3J | ○ | KOA | 1005 | 3.3 | ±5% | 0.063W
RK73H1ETTP3R60F | ○ | KOA | 1005 | 3.6 | ±1% | 0.063W
RK73B1ETTP3R6J | ○ | KOA | 1005 | 3.6 | ±5% | 0.063W
RK73H1ETTP3R90F | ○ | KOA | 1005 | 3.9 | ±1% | 0.063W
RK73B1ETTP3R9J | ○ | KOA | 1005 | 3.9 | ±5% | 0.063W
RK73H1ETTP4R30F | ○ | KOA | 1005 | 4.3 | ±1% | 0.063W
RK73B1ETTP4R3J | ○ | KOA | 1005 | 4.3 | ±5% | 0.063W
RK73H1ETTP4R70F | ○ | KOA | 1005 | 4.7 | ±1% | 0.063W
RK73B1ETTP4R7J | ○ | KOA | 1005 | 4.7 | ±5% | 0.063W
RK73H1ETTP5R10F | ○ | KOA | 1005 | 5.1 | ±1% | 0.063W
RK73B1ETTP5R1J | ○ | KOA | 1005 | 5.1 | ±5% | 0.063W
RK73H1ETTP5R60F | ○ | KOA | 1005 | 5.6 | ±1% | 0.063W
RK73B1ETTP5R6J | ○ | KOA | 1005 | 5.6 | ±5% | 0.063W
RK73H1ETTP6R20F | ○ | KOA | 1005 | 6.2 | ±1% | 0.063W
RK73B1ETTP6R2J | ○ | KOA | 1005 | 6.2 | ±5% | 0.063W
RK73H1ETTP6R80F | ○ | KOA | 1005 | 6.8 | ±1% | 0.063W
RK73B1ETTP6R8J | ○ | KOA | 1005 | 6.8 | ±5% | 0.063W
RK73H1ETTP7R50F | ○ | KOA | 1005 | 7.5 | ±1% | 0.063W
RK73B1ETTP7R5J | ○ | KOA | 1005 | 7.5 | ±5% | 0.063W
RK73H1ETTP8R20F | ○ | KOA | 1005 | 8.2 | ±1% | 0.063W
RK73B1ETTP8R2J | ○ | KOA | 1005 | 8.2 | ±5% | 0.063W
RK73H1ETTP9R10F | ○ | KOA | 1005 | 9.1 | ±1% | 0.063W
RK73B1ETTP9R1J | ○ | KOA | 1005 | 9.1 | ±5% | 0.063W
RK73H1ETTP10R0F | ○ | KOA | 1005 | 10 | ±1% | 0.063W
RK73B1ETTP100J | ○ | KOA | 1005 | 10 | ±5% | 0.063W
RK73H1ETTP11R0F | ○ | KOA | 1005 | 11 | ±1% | 0.063W
RK73B1ETTP110J | ○ | KOA | 1005 | 11 | ±5% | 0.063W
RK73H1ETTP12R0F | ○ | KOA | 1005 | 12 | ±1% | 0.063W
RK73B1ETTP120J | ○ | KOA | 1005 | 12 | ±5% | 0.063W
RK73H1ETTP13R0F | ○ | KOA | 1005 | 13 | ±1% | 0.063W
RK73B1ETTP130J | ○ | KOA | 1005 | 13 | ±5% | 0.063W
RK73H1ETTP15R0F | ○ | KOA | 1005 | 15 | ±1% | 0.063W
RK73B1ETTP150J | ○ | KOA | 1005 | 15 | ±5% | 0.063W
RK73H1ETTP16R0F | ○ | KOA | 1005 | 16 | ±1% | 0.063W
RK73B1ETTP160J | ○ | KOA | 1005 | 16 | ±5% | 0.063W
RK73H1ETTP18R0F | ○ | KOA | 1005 | 18 | ±1% | 0.063W
RK73B1ETTP180J | ○ | KOA | 1005 | 18 | ±5% | 0.063W
RK73H1ETTP20R0F | ○ | KOA | 1005 | 20 | ±1% | 0.063W
RK73B1ETTP200J | ○ | KOA | 1005 | 20 | ±5% | 0.063W
RK73H1ETTP22R0F | ○ | KOA | 1005 | 22 | ±1% | 0.063W
RK73B1ETTP220J | ○ | KOA | 1005 | 22 | ±5% | 0.063W
RK73H1ETTP24R0F | ○ | KOA | 1005 | 24 | ±1% | 0.063W
RK73B1ETTP240J | ○ | KOA | 1005 | 24 | ±5% | 0.063W
RK73H1ETTP27R0F | ○ | KOA | 1005 | 27 | ±1% | 0.063W
RK73B1ETTP270J | ○ | KOA | 1005 | 27 | ±5% | 0.063W
RK73H1ETTP30R0F | ○ | KOA | 1005 | 30 | ±1% | 0.063W
RK73B1ETTP300J | ○ | KOA | 1005 | 30 | ±5% | 0.063W
RK73H1ETTP33R0F | ○ | KOA | 1005 | 33 | ±1% | 0.063W
RK73B1ETTP330J | ○ | KOA | 1005 | 33 | ±5% | 0.063W
RK73H1ETTP36R0F | ○ | KOA | 1005 | 36 | ±1% | 0.063W
RK73B1ETTP360J | ○ | KOA | 1005 | 36 | ±5% | 0.063W
RK73H1ETTP39R0F | ○ | KOA | 1005 | 39 | ±1% | 0.063W
RK73B1ETTP390J | ○ | KOA | 1005 | 39 | ±5% | 0.063W
RK73H1ETTP43R0F | ○ | KOA | 1005 | 43 | ±1% | 0.063W
RK73B1ETTP430J | ○ | KOA | 1005 | 43 | ±5% | 0.063W
RK73H1ETTP47R0F | ○ | KOA | 1005 | 47 | ±1% | 0.063W
RK73B1ETTP470J | ○ | KOA | 1005 | 47 | ±5% | 0.063W
RK73H1ETTP51R0F | ○ | KOA | 1005 | 51 | ±1% | 0.063W
RK73B1ETTP510J | ○ | KOA | 1005 | 51 | ±5% | 0.063W
RK73H1ETTP56R0F | ○ | KOA | 1005 | 56 | ±1% | 0.063W
RK73B1ETTP560J | ○ | KOA | 1005 | 56 | ±5% | 0.063W
RK73H1ETTP62R0F | ○ | KOA | 1005 | 62 | ±1% | 0.063W
RK73B1ETTP620J | ○ | KOA | 1005 | 62 | ±5% | 0.063W
RK73H1ETTP68R0F | ○ | KOA | 1005 | 68 | ±1% | 0.063W
RK73B1ETTP680J | ○ | KOA | 1005 | 68 | ±5% | 0.063W
RK73H1ETTP75R0F | ○ | KOA | 1005 | 75 | ±1% | 0.063W
RK73B1ETTP750J | ○ | KOA | 1005 | 75 | ±5% | 0.063W
RK73H1ETTP82R0F | ○ | KOA | 1005 | 82 | ±1% | 0.063W
RK73B1ETTP820J | ○ | KOA | 1005 | 82 | ±5% | 0.063W
RK73H1ETTP91R0F | ○ | KOA | 1005 | 91 | ±1% | 0.063W
RK73B1ETTP910J | ○ | KOA | 1005 | 91 | ±5% | 0.063W
RK73H1ETTP1000F | ○ | KOA | 1005 | 100 | ±1% | 0.063W
RK73B1ETTP101J | ○ | KOA | 1005 | 100 | ±5% | 0.063W
RK73H1ETTP1100F | ○ | KOA | 1005 | 110 | ±1% | 0.063W
RK73B1ETTP111J | ○ | KOA | 1005 | 110 | ±5% | 0.063W
RK73H1ETTP1200F | ○ | KOA | 1005 | 120 | ±1% | 0.063W
RK73B1ETTP121J | ○ | KOA | 1005 | 120 | ±5% | 0.063W
RK73H1ETTP1300F | ○ | KOA | 1005 | 130 | ±1% | 0.063W
RK73B1ETTP131J | ○ | KOA | 1005 | 130 | ±5% | 0.063W
RK73H1ETTP1500F | ○ | KOA | 1005 | 150 | ±1% | 0.063W
RK73B1ETTP151J | ○ | KOA | 1005 | 150 | ±5% | 0.063W
RK73H1ETTP1600F | ○ | KOA | 1005 | 160 | ±1% | 0.063W
RK73B1ETTP161J | ○ | KOA | 1005 | 160 | ±5% | 0.063W
RK73H1ETTP1800F | ○ | KOA | 1005 | 180 | ±1% | 0.063W
RK73B1ETTP181J | ○ | KOA | 1005 | 180 | ±5% | 0.063W
RK73H1ETTP2000F | ○ | KOA | 1005 | 200 | ±1% | 0.063W
RK73B1ETTP201J | ○ | KOA | 1005 | 200 | ±5% | 0.063W
RK73H1ETTP2200F | ○ | KOA | 1005 | 220 | ±1% | 0.063W
RK73B1ETTP221J | ○ | KOA | 1005 | 220 | ±5% | 0.063W
RK73H1ETTP2400F | ○ | KOA | 1005 | 240 | ±1% | 0.063W
RK73B1ETTP241J | ○ | KOA | 1005 | 240 | ±5% | 0.063W
RK73H1ETTP2700F | ○ | KOA | 1005 | 270 | ±1% | 0.063W
RK73B1ETTP271J | ○ | KOA | 1005 | 270 | ±5% | 0.063W
RK73H1ETTP3000F | ○ | KOA | 1005 | 300 | ±1% | 0.063W
RK73B1ETTP301J | ○ | KOA | 1005 | 300 | ±5% | 0.063W
RK73H1ETTP3300F | ○ | KOA | 1005 | 330 | ±1% | 0.063W
RK73B1ETTP331J | ○ | KOA | 1005 | 330 | ±5% | 0.063W
RK73H1ETTP3600F | ○ | KOA | 1005 | 360 | ±1% | 0.063W
RK73B1ETTP361J | ○ | KOA | 1005 | 360 | ±5% | 0.063W
RK73H1ETTP3900F | ○ | KOA | 1005 | 390 | ±1% | 0.063W
RK73B1ETTP391J | ○ | KOA | 1005 | 390 | ±5% | 0.063W
RK73H1ETTP4300F | ○ | KOA | 1005 | 430 | ±1% | 0.063W
RK73B1ETTP431J | ○ | KOA | 1005 | 430 | ±5% | 0.063W
RK73H1ETTP4700F | ○ | KOA | 1005 | 470 | ±1% | 0.063W
RK73B1ETTP471J | ○ | KOA | 1005 | 470 | ±5% | 0.063W
RK73H1ETTP5100F | ○ | KOA | 1005 | 510 | ±1% | 0.063W
RK73B1ETTP511J | ○ | KOA | 1005 | 510 | ±5% | 0.063W
RK73H1ETTP5600F | ○ | KOA | 1005 | 560 | ±1% | 0.063W
RK73B1ETTP561J | ○ | KOA | 1005 | 560 | ±5% | 0.063W
RK73H1ETTP6200F | ○ | KOA | 1005 | 620 | ±1% | 0.063W
RK73B1ETTP621J | ○ | KOA | 1005 | 620 | ±5% | 0.063W
RK73H1ETTP6800F | ○ | KOA | 1005 | 680 | ±1% | 0.063W
RK73B1ETTP681J | ○ | KOA | 1005 | 680 | ±5% | 0.063W
RK73H1ETTP7500F | ○ | KOA | 1005 | 750 | ±1% | 0.063W
RK73B1ETTP751J | ○ | KOA | 1005 | 750 | ±5% | 0.063W
RK73H1ETTP8200F | ○ | KOA | 1005 | 820 | ±1% | 0.063W
RK73B1ETTP821J | ○ | KOA | 1005 | 820 | ±5% | 0.063W
RK73H1ETTP9100F | ○ | KOA | 1005 | 910 | ±1% | 0.063W
RK73B1ETTP911J | ○ | KOA | 1005 | 910 | ±5% | 0.063W
RK73H1ETTP1001F | ○ | KOA | 1005 | 1.00k | ±1% | 0.063W
RK73B1ETTP102J | ○ | KOA | 1005 | 1k | ±5% | 0.063W
RK73H1ETTP1101F | ○ | KOA | 1005 | 1.10k | ±1% | 0.063W
RK73B1ETTP112J | ○ | KOA | 1005 | 1.1k | ±5% | 0.063W
RK73H1ETTP1201F | ○ | KOA | 1005 | 1.20k | ±1% | 0.063W
RK73B1ETTP122J | ○ | KOA | 1005 | 1.2k | ±5% | 0.063W
RK73H1ETTP1301F | ○ | KOA | 1005 | 1.30k | ±1% | 0.063W
RK73B1ETTP132J | ○ | KOA | 1005 | 1.3k | ±5% | 0.063W
RK73H1ETTP1501F | ○ | KOA | 1005 | 1.50k | ±1% | 0.063W
RK73B1ETTP152J | ○ | KOA | 1005 | 1.5k | ±5% | 0.063W
RK73H1ETTP1601F | ○ | KOA | 1005 | 1.60k | ±1% | 0.063W
RK73B1ETTP162J | ○ | KOA | 1005 | 1.6k | ±5% | 0.063W
RK73H1ETTP1801F | ○ | KOA | 1005 | 1.80k | ±1% | 0.063W
RK73B1ETTP182J | ○ | KOA | 1005 | 1.8k | ±5% | 0.063W
RK73H1ETTP2001F | ○ | KOA | 1005 | 2.00k | ±1% | 0.063W
RK73B1ETTP202J | ○ | KOA | 1005 | 2.0k | ±5% | 0.063W
RK73H1ETTP2201F | ○ | KOA | 1005 | 2.20k | ±1% | 0.063W
RK73B1ETTP222J | ○ | KOA | 1005 | 2.2k | ±5% | 0.063W
RK73H1ETTP2401F | ○ | KOA | 1005 | 2.40k | ±1% | 0.063W
RK73B1ETTP242J | ○ | KOA | 1005 | 2.4k | ±5% | 0.063W
RK73H1ETTP2701F | ○ | KOA | 1005 | 2.70k | ±1% | 0.063W
RK73B1ETTP272J | ○ | KOA | 1005 | 2.7k | ±5% | 0.063W
RK73H1ETTP3001F | ○ | KOA | 1005 | 3.00k | ±1% | 0.063W
RK73B1ETTP302J | ○ | KOA | 1005 | 3.0k | ±5% | 0.063W
RK73H1ETTP3301F | ○ | KOA | 1005 | 3.30k | ±1% | 0.063W
RK73B1ETTP332J | ○ | KOA | 1005 | 3.3k | ±5% | 0.063W
RK73H1ETTP3601F | ○ | KOA | 1005 | 3.60k | ±1% | 0.063W
RK73B1ETTP362J | ○ | KOA | 1005 | 3.6k | ±5% | 0.063W
RK73H1ETTP3901F | ○ | KOA | 1005 | 3.90k | ±1% | 0.063W
RK73B1ETTP392J | ○ | KOA | 1005 | 3.9k | ±5% | 0.063W
RK73H1ETTP4301F | ○ | KOA | 1005 | 4.30k | ±1% | 0.063W
RK73B1ETTP432J | ○ | KOA | 1005 | 4.3k | ±5% | 0.063W
RK73H1ETTP4701F | ○ | KOA | 1005 | 4.70k | ±1% | 0.063W
RK73B1ETTP472J | ○ | KOA | 1005 | 4.7k | ±5% | 0.063W
RK73H1ETTP5101F | ○ | KOA | 1005 | 5.10k | ±1% | 0.063W
RK73B1ETTP512J | ○ | KOA | 1005 | 5.1k | ±5% | 0.063W
RK73H1ETTP5601F | ○ | KOA | 1005 | 5.60k | ±1% | 0.063W
RK73B1ETTP562J | ○ | KOA | 1005 | 5.6k | ±5% | 0.063W
RK73H1ETTP6201F | ○ | KOA | 1005 | 6.20k | ±1% | 0.063W
RK73B1ETTP622J | ○ | KOA | 1005 | 6.2k | ±5% | 0.063W
RK73H1ETTP6801F | ○ | KOA | 1005 | 6.80k | ±1% | 0.063W
RK73B1ETTP682J | ○ | KOA | 1005 | 6.8k | ±5% | 0.063W
RK73H1ETTP7501F | ○ | KOA | 1005 | 7.50k | ±1% | 0.063W
RK73B1ETTP752J | ○ | KOA | 1005 | 7.5k | ±5% | 0.063W
RK73H1ETTP8201F | ○ | KOA | 1005 | 8.20k | ±1% | 0.063W
RK73B1ETTP822J | ○ | KOA | 1005 | 8.2k | ±5% | 0.063W
RK73H1ETTP9101F | ○ | KOA | 1005 | 9.10k | ±1% | 0.063W
RK73B1ETTP912J | ○ | KOA | 1005 | 9.1k | ±5% | 0.063W
RK73H1ETTP1002F | ○ | KOA | 1005 | 10.0k | ±1% | 0.063W
RK73B1ETTP103J | ○ | KOA | 1005 | 10k | ±5% | 0.063W
RK73H1ETTP1102F | ○ | KOA | 1005 | 11.0k | ±1% | 0.063W
RK73B1ETTP113J | ○ | KOA | 1005 | 11k | ±5% | 0.063W
RK73H1ETTP1202F | ○ | KOA | 1005 | 12.0k | ±1% | 0.063W
RK73B1ETTP123J | ○ | KOA | 1005 | 12k | ±5% | 0.063W
RK73H1ETTP1302F | ○ | KOA | 1005 | 13.0k | ±1% | 0.063W
RK73B1ETTP133J | ○ | KOA | 1005 | 13k | ±5% | 0.063W
RK73H1ETTP1502F | ○ | KOA | 1005 | 15.0k | ±1% | 0.063W
RK73B1ETTP153J | ○ | KOA | 1005 | 15k | ±5% | 0.063W
RK73H1ETTP1602F | ○ | KOA | 1005 | 16.0k | ±1% | 0.063W
RK73B1ETTP163J | ○ | KOA | 1005 | 16k | ±5% | 0.063W
RK73H1ETTP1802F | ○ | KOA | 1005 | 18.0k | ±1% | 0.063W
RK73B1ETTP183J | ○ | KOA | 1005 | 18k | ±5% | 0.063W
RK73H1ETTP2002F | ○ | KOA | 1005 | 20.0k | ±1% | 0.063W
RK73B1ETTP203J | ○ | KOA | 1005 | 20k | ±5% | 0.063W
RK73H1ETTP2202F | ○ | KOA | 1005 | 22.0k | ±1% | 0.063W
RK73B1ETTP223J | ○ | KOA | 1005 | 22k | ±5% | 0.063W
RK73H1ETTP2402F | ○ | KOA | 1005 | 24.0k | ±1% | 0.063W
RK73B1ETTP243J | ○ | KOA | 1005 | 24k | ±5% | 0.063W
RK73H1ETTP2702F | ○ | KOA | 1005 | 27.0k | ±1% | 0.063W
RK73B1ETTP273J | ○ | KOA | 1005 | 27k | ±5% | 0.063W
RK73H1ETTP3002F | ○ | KOA | 1005 | 30.0k | ±1% | 0.063W
RK73B1ETTP303J | ○ | KOA | 1005 | 30k | ±5% | 0.063W
RK73H1ETTP3302F | ○ | KOA | 1005 | 33.0k | ±1% | 0.063W
RK73B1ETTP333J | ○ | KOA | 1005 | 33k | ±5% | 0.063W
RK73H1ETTP3602F | ○ | KOA | 1005 | 36.0k | ±1% | 0.063W
RK73B1ETTP363J | ○ | KOA | 1005 | 36k | ±5% | 0.063W
RK73H1ETTP3902F | ○ | KOA | 1005 | 39.0k | ±1% | 0.063W
RK73B1ETTP393J | ○ | KOA | 1005 | 39k | ±5% | 0.063W
RK73H1ETTP4302F | ○ | KOA | 1005 | 43.0k | ±1% | 0.063W
RK73B1ETTP433J | ○ | KOA | 1005 | 43k | ±5% | 0.063W
RK73H1ETTP4702F | ○ | KOA | 1005 | 47.0k | ±1% | 0.063W
RK73B1ETTP473J | ○ | KOA | 1005 | 47k | ±5% | 0.063W
RK73H1ETTP5102F | ○ | KOA | 1005 | 51.0k | ±1% | 0.063W
RK73B1ETTP513J | ○ | KOA | 1005 | 51k | ±5% | 0.063W
RK73H1ETTP5602F | ○ | KOA | 1005 | 56.0k | ±1% | 0.063W
RK73B1ETTP563J | ○ | KOA | 1005 | 56k | ±5% | 0.063W
RK73H1ETTP6202F | ○ | KOA | 1005 | 62.0k | ±1% | 0.063W
RK73B1ETTP623J | ○ | KOA | 1005 | 62k | ±5% | 0.063W
RK73H1ETTP6802F | ○ | KOA | 1005 | 68.0k | ±1% | 0.063W
RK73B1ETTP683J | ○ | KOA | 1005 | 68k | ±5% | 0.063W
RK73H1ETTP7502F | ○ | KOA | 1005 | 75.0k | ±1% | 0.063W
RK73B1ETTP753J | ○ | KOA | 1005 | 75k | ±5% | 0.063W
RK73H1ETTP8202F | ○ | KOA | 1005 | 82.0k | ±1% | 0.063W
RK73B1ETTP823J | ○ | KOA | 1005 | 82k | ±5% | 0.063W
RK73H1ETTP9102F | ○ | KOA | 1005 | 91.0k | ±1% | 0.063W
RK73B1ETTP913J | ○ | KOA | 1005 | 91k | ±5% | 0.063W
RK73H1ETTP1003F | ○ | KOA | 1005 | 100k | ±1% | 0.063W
RK73B1ETTP104J | ○ | KOA | 1005 | 100k | ±5% | 0.063W
RK73H1ETTP1103F | ○ | KOA | 1005 | 110k | ±1% | 0.063W
RK73B1ETTP114J | ○ | KOA | 1005 | 110k | ±5% | 0.063W
RK73H1ETTP1203F | ○ | KOA | 1005 | 120k | ±1% | 0.063W
RK73B1ETTP124J | ○ | KOA | 1005 | 120k | ±5% | 0.063W
RK73H1ETTP1303F | ○ | KOA | 1005 | 130k | ±1% | 0.063W
RK73B1ETTP134J | ○ | KOA | 1005 | 130k | ±5% | 0.063W
RK73H1ETTP1503F | ○ | KOA | 1005 | 150k | ±1% | 0.063W
RK73B1ETTP154J | ○ | KOA | 1005 | 150k | ±5% | 0.063W
RK73H1ETTP1603F | ○ | KOA | 1005 | 160k | ±1% | 0.063W
RK73B1ETTP164J | ○ | KOA | 1005 | 160k | ±5% | 0.063W
RK73H1ETTP1803F | ○ | KOA | 1005 | 180k | ±1% | 0.063W
RK73B1ETTP184J | ○ | KOA | 1005 | 180k | ±5% | 0.063W
RK73H1ETTP2003F | ○ | KOA | 1005 | 200k | ±1% | 0.063W
RK73B1ETTP204J | ○ | KOA | 1005 | 200k | ±5% | 0.063W
RK73H1ETTP2203F | ○ | KOA | 1005 | 220k | ±1% | 0.063W
RK73B1ETTP224J | ○ | KOA | 1005 | 220k | ±5% | 0.063W
RK73H1ETTP2403F | ○ | KOA | 1005 | 240k | ±1% | 0.063W
RK73B1ETTP244J | ○ | KOA | 1005 | 240k | ±5% | 0.063W
RK73H1ETTP2703F | ○ | KOA | 1005 | 270k | ±1% | 0.063W
RK73B1ETTP274J | ○ | KOA | 1005 | 270k | ±5% | 0.063W
RK73H1ETTP3003F | ○ | KOA | 1005 | 300k | ±1% | 0.063W
RK73B1ETTP304J | ○ | KOA | 1005 | 300k | ±5% | 0.063W
RK73H1ETTP3303F | ○ | KOA | 1005 | 330k | ±1% | 0.063W
RK73B1ETTP334J | ○ | KOA | 1005 | 330k | ±5% | 0.063W
RK73H1ETTP3603F | ○ | KOA | 1005 | 360k | ±1% | 0.063W
RK73B1ETTP364J | ○ | KOA | 1005 | 360k | ±5% | 0.063W
RK73H1ETTP3903F | ○ | KOA | 1005 | 390k | ±1% | 0.063W
RK73B1ETTP394J | ○ | KOA | 1005 | 390k | ±5% | 0.063W
RK73H1ETTP4303F | ○ | KOA | 1005 | 430k | ±1% | 0.063W
RK73B1ETTP434J | ○ | KOA | 1005 | 430k | ±5% | 0.063W
RK73H1ETTP4703F | ○ | KOA | 1005 | 470k | ±1% | 0.063W
RK73B1ETTP474J | ○ | KOA | 1005 | 470k | ±5% | 0.063W
RK73H1ETTP5103F | ○ | KOA | 1005 | 510k | ±1% | 0.063W
RK73B1ETTP514J | ○ | KOA | 1005 | 510k | ±5% | 0.063W
RK73H1ETTP5603F | ○ | KOA | 1005 | 560k | ±1% | 0.063W
RK73B1ETTP564J | ○ | KOA | 1005 | 560k | ±5% | 0.063W
RK73H1ETTP6203F | ○ | KOA | 1005 | 620k | ±1% | 0.063W
RK73B1ETTP624J | ○ | KOA | 1005 | 620k | ±5% | 0.063W
RK73H1ETTP6803F | ○ | KOA | 1005 | 680k | ±1% | 0.063W
RK73B1ETTP684J | ○ | KOA | 1005 | 680k | ±5% | 0.063W
RK73H1ETTP7503F | ○ | KOA | 1005 | 750k | ±1% | 0.063W
RK73B1ETTP754J | ○ | KOA | 1005 | 750k | ±5% | 0.063W
RK73H1ETTP8203F | ○ | KOA | 1005 | 820k | ±1% | 0.063W
RK73B1ETTP824J | ○ | KOA | 1005 | 820k | ±5% | 0.063W
RK73H1ETTP9103F | ○ | KOA | 1005 | 910k | ±1% | 0.063W
RK73B1ETTP914J | ○ | KOA | 1005 | 910k | ±5% | 0.063W
RK73H1ETTP1004F | ○ | KOA | 1005 | 1.00M | ±1% | 0.063W
RK73B1ETTP105J | ○ | KOA | 1005 | 1M | ±5% | 0.063W
RK73H1ETTP1104F | ○ | KOA | 1005 | 1.10M | ±1% | 0.063W
RK73B1ETTP115J | ○ | KOA | 1005 | 1.1M | ±5% | 0.063W
RK73H1ETTP1204F | ○ | KOA | 1005 | 1.20M | ±1% | 0.063W
RK73B1ETTP125J | ○ | KOA | 1005 | 1.2M | ±5% | 0.063W
RK73H1ETTP1304F | ○ | KOA | 1005 | 1.30M | ±1% | 0.063W
RK73B1ETTP135J | ○ | KOA | 1005 | 1.3M | ±5% | 0.063W
RK73H1ETTP1504F | ○ | KOA | 1005 | 1.50M | ±1% | 0.063W
RK73B1ETTP155J | ○ | KOA | 1005 | 1.5M | ±5% | 0.063W
RK73H1ETTP1604F | ○ | KOA | 1005 | 1.60M | ±1% | 0.063W
RK73B1ETTP165J | ○ | KOA | 1005 | 1.6M | ±5% | 0.063W
RK73H1ETTP1804F | ○ | KOA | 1005 | 1.80M | ±1% | 0.063W
RK73B1ETTP185J | ○ | KOA | 1005 | 1.8M | ±5% | 0.063W
RK73H1ETTP2004F | ○ | KOA | 1005 | 2.00M | ±1% | 0.063W
RK73B1ETTP205J | ○ | KOA | 1005 | 2.0M | ±5% | 0.063W
RK73H1ETTP2204F | ○ | KOA | 1005 | 2.2M | ±1% | 0.063W
RK73B1ETTP225J | ○ | KOA | 1005 | 2.2M | ±5% | 0.063W
RK73H1ETTP2404F | ○ | KOA | 1005 | 2.4M | ±1% | 0.063W
RK73B1ETTP245J | ○ | KOA | 1005 | 2.4M | ±5% | 0.063W
RK73H1ETTP2704F | ○ | KOA | 1005 | 2.70M | ±1% | 0.063W
RK73B1ETTP275J | ○ | KOA | 1005 | 2.7M | ±5% | 0.063W
RK73H1ETTP3004F | ○ | KOA | 1005 | 3.00M | ±1% | 0.063W
RK73B1ETTP305J | ○ | KOA | 1005 | 3.0M | ±5% | 0.063W
RK73H1ETTP3304F | ○ | KOA | 1005 | 3.30M | ±1% | 0.063W
RK73B1ETTP335J | ○ | KOA | 1005 | 3.3M | ±5% | 0.063W
RK73H1ETTP3604F | ○ | KOA | 1005 | 3.60M | ±1% | 0.063W
RK73B1ETTP365J | ○ | KOA | 1005 | 3.6M | ±5% | 0.063W
RK73H1ETTP3904F | ○ | KOA | 1005 | 3.90M | ±1% | 0.063W
RK73B1ETTP395J | ○ | KOA | 1005 | 3.9M | ±5% | 0.063W
RK73H1ETTP4304F | ○ | KOA | 1005 | 4.30M | ±1% | 0.063W
RK73B1ETTP435J | ○ | KOA | 1005 | 4.3M | ±5% | 0.063W
RK73H1ETTP4704F | ○ | KOA | 1005 | 4.70M | ±1% | 0.063W
RK73B1ETTP475J | ○ | KOA | 1005 | 4.7M | ±5% | 0.063W
RK73H1ETTP5104F | ○ | KOA | 1005 | 5.10M | ±1% | 0.063W
RK73B1ETTP515J | ○ | KOA | 1005 | 5.1M | ±5% | 0.063W
RK73H1ETTP5604F | ○ | KOA | 1005 | 5.60M | ±1% | 0.063W
RK73B1ETTP565J | ○ | KOA | 1005 | 5.6M | ±5% | 0.063W
RK73H1ETTP6204F | ○ | KOA | 1005 | 6.20M | ±1% | 0.063W
RK73B1ETTP625J | ○ | KOA | 1005 | 6.2M | ±5% | 0.063W
RK73H1ETTP6804F | ○ | KOA | 1005 | 6.80M | ±1% | 0.063W
RK73B1ETTP685J | ○ | KOA | 1005 | 6.8M | ±5% | 0.063W
RK73H1ETTP7504F | ○ | KOA | 1005 | 7.50M | ±1% | 0.063W
RK73B1ETTP755J | ○ | KOA | 1005 | 7.5M | ±5% | 0.063W
RK73H1ETTP8204F | ○ | KOA | 1005 | 8.20M | ±1% | 0.063W
RK73B1ETTP825J | ○ | KOA | 1005 | 8.2M | ±5% | 0.063W
RK73H1ETTP9104F | ○ | KOA | 1005 | 9.10M | ±1% | 0.063W
RK73B1ETTP915J | ○ | KOA | 1005 | 9.1M | ±5% | 0.063W
RK73H1ETTP1005F | ○ | KOA | 1005 | 10.0M | ±1% | 0.063W
RK73B1ETTP106J | ○ | KOA | 1005 | 10M | ±5% | 0.063W
RK73Z1JTTD | ○ | KOA | 1608 | 0 |  | 1A
RK73H1JTTD1R00F | ○ | KOA | 1608 | 1 | ±1% | 0.1W
RK73B1JTTD1R0J | ○ | KOA | 1608 | 1 | ±5% | 0.1W
RK73H1JTTD1R10F | ○ | KOA | 1608 | 1.1 | ±1% | 0.1W
RK73B1JTTD1R1J | ○ | KOA | 1608 | 1.1 | ±5% | 0.1W
RK73H1JTTD1R20F | ○ | KOA | 1608 | 1.2 | ±1% | 0.1W
RK73B1JTTD1R2J | ○ | KOA | 1608 | 1.2 | ±5% | 0.1W
RK73H1JTTD1R30F | ○ | KOA | 1608 | 1.3 | ±1% | 0.1W
RK73B1JTTD1R3J | ○ | KOA | 1608 | 1.3 | ±5% | 0.1W
RK73H1JTTD1R50F | ○ | KOA | 1608 | 1.5 | ±1% | 0.1W
RK73B1JTTD1R5J | ○ | KOA | 1608 | 1.5 | ±5% | 0.1W
RK73H1JTTD1R60F | ○ | KOA | 1608 | 1.6 | ±1% | 0.1W
RK73B1JTTD1R6J | ○ | KOA | 1608 | 1.6 | ±5% | 0.1W
RK73H1JTTD1R80F | ○ | KOA | 1608 | 1.8 | ±1% | 0.1W
RK73B1JTTD1R8J | ○ | KOA | 1608 | 1.8 | ±5% | 0.1W
RK73H1JTTD2R00F | ○ | KOA | 1608 | 2 | ±1% | 0.1W
RK73B1JTTD2R0J | ○ | KOA | 1608 | 2 | ±5% | 0.1W
RK73H1JTTD2R20F | ○ | KOA | 1608 | 2.2 | ±1% | 0.1W
RK73B1JTTD2R2J | ○ | KOA | 1608 | 2.2 | ±5% | 0.1W
RK73H1JTTD2R40F | ○ | KOA | 1608 | 2.4 | ±1% | 0.1W
RK73B1JTTD2R4J | ○ | KOA | 1608 | 2.4 | ±5% | 0.1W
RK73H1JTTD2R70F | ○ | KOA | 1608 | 2.7 | ±1% | 0.1W
RK73B1JTTD2R7J | ○ | KOA | 1608 | 2.7 | ±5% | 0.1W
RK73H1JTTD3R00F | ○ | KOA | 1608 | 3 | ±1% | 0.1W
RK73B1JTTD3R0J | ○ | KOA | 1608 | 3 | ±5% | 0.1W
RK73H1JTTD3R30F | ○ | KOA | 1608 | 3.3 | ±1% | 0.1W
RK73B1JTTD3R3J | ○ | KOA | 1608 | 3.3 | ±5% | 0.1W
RK73H1JTTD3R60F | ○ | KOA | 1608 | 3.6 | ±1% | 0.1W
RK73B1JTTD3R6J | ○ | KOA | 1608 | 3.6 | ±5% | 0.1W
RK73H1JTTD3R90F | ○ | KOA | 1608 | 3.9 | ±1% | 0.1W
RK73B1JTTD3R9J | ○ | KOA | 1608 | 3.9 | ±5% | 0.1W
RK73H1JTTD4R30F | ○ | KOA | 1608 | 4.3 | ±1% | 0.1W
RK73B1JTTD4R3J | ○ | KOA | 1608 | 4.3 | ±5% | 0.1W
RK73H1JTTD4R70F | ○ | KOA | 1608 | 4.7 | ±1% | 0.1W
RK73B1JTTD4R7J | ○ | KOA | 1608 | 4.7 | ±5% | 0.1W
RK73H1JTTD5R10F | ○ | KOA | 1608 | 5.1 | ±1% | 0.1W
RK73B1JTTD5R1J | ○ | KOA | 1608 | 5.1 | ±5% | 0.1W
RK73H1JTTD5R60F | ○ | KOA | 1608 | 5.6 | ±1% | 0.1W
RK73B1JTTD5R6J | ○ | KOA | 1608 | 5.6 | ±5% | 0.1W
RK73H1JTTD6R20F | ○ | KOA | 1608 | 6.2 | ±1% | 0.1W
RK73B1JTTD6R2J | ○ | KOA | 1608 | 6.2 | ±5% | 0.1W
RK73H1JTTD6R80F | ○ | KOA | 1608 | 6.8 | ±1% | 0.1W
RK73B1JTTD6R8J | ○ | KOA | 1608 | 6.8 | ±5% | 0.1W
RK73H1JTTD7R50F | ○ | KOA | 1608 | 7.5 | ±1% | 0.1W
RK73B1JTTD7R5J | ○ | KOA | 1608 | 7.5 | ±5% | 0.1W
RK73H1JTTD8R20F | ○ | KOA | 1608 | 8.2 | ±1% | 0.1W
RK73B1JTTD8R2J | ○ | KOA | 1608 | 8.2 | ±5% | 0.1W
RK73H1JTTD9R10F | ○ | KOA | 1608 | 9.1 | ±1% | 0.1W
RK73B1JTTD9R1J | ○ | KOA | 1608 | 9.1 | ±5% | 0.1W
RK73H1JTTD10R0F | ○ | KOA | 1608 | 10 | ±1% | 0.1W
RK73B1JTTD100J | ○ | KOA | 1608 | 10 | ±5% | 0.1W
RK73H1JTTD11R0F | ○ | KOA | 1608 | 11 | ±1% | 0.1W
RK73B1JTTD110J | ○ | KOA | 1608 | 11 | ±5% | 0.1W
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

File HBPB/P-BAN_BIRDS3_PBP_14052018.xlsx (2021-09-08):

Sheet: 必ずお読みください
入力項目説明
メ ー カ ー |  |  | 電子部品のメーカー名をご入力ください。
部 品 種 別 |  |  | 電子部品の種別をご入力ください。例：チップ抵抗、トランジスタ、LED、など
電 子 部 品 型 番 |  |  | 電子部品の型番をご入力ください。 ※誤表記による不具合を回避するためにも正確なご入力をお願い致します。 ※表面実装の抵抗やコンデンサ(電解、タンタル以外)は、後述「電子部品見取り表」をご参照のうえ、ご入力ください。
配 置 記 号 / リファレンス |  |  | シルク図/配置図に表記された配置記号/リファレンス番号をご入力ください。 ※複数入力する場合は、カンマ「,」区切りでのご入力をお願い致します。 ※電子部品型番ベースでのご記入をお願い致します。（１つの電子部品型番に対して、配置番号を複数記入）
個 数 |  |  | 電子部品の個数をご入力ください。
ピ ン 数 |  |  | 電子部品の総ピン数をご入力ください。 ※基板取付穴、部品取付穴、全てのスルー・ノンスルーホール、面実装部品のパッド、及び次の①～⑤の配線を伴う箇所（①テストピン、②チェックランド、③引き出しランド、④ジャンパピン、⑤入出力ランドの総計。
実装 / 未実装 |  |  | 実装サービスでの「実装」/「未実装」をご選択ください。 ※同じ電子部品型番の中で実装と未実装が分かれる場合は、それぞれ2行に分けて配置記号をご入力ください。
部品分類 | SMD |  | 表面実装部品
 | DIP |  | 挿入部品
 | 特殊 BGA等 |  | BGA/CSP/LGA/QFNなど部品極性が部品の真下に配置された部品 -BGA：Ball Grid Array/下面に半田ボールの端子を配置したパッケージ。 -CSP：Chip Size Package/チッププサイズと同じか、もしくは僅かに大きいパッケージ。 -LGA：Land Grid Array/裏面に外部入出力用のランドを設けたパッケージ。※BGAの半田ボールがない。 -QFN：Quad Flat Non-Lead Package/QFPに似ていますが、外部入出力用のピンが出ていないパッケージ。
P板.com提供部品 (無料) |  |  | 【無償提供部品一覧】シートに記載されている「メーカー型番」を【部品リスト入力フォーム】シートのD列（電子部品型番）に入力し、I列（実装／未実装）を「実装」に設定いただくと、自動的に「○」が表示されます。 ※無料提供部品：チップコンデンサ/チップ抵抗を約1000種、実装サービスをご利用のお客様に無料提供いたします。 ※「○」が付かない場合は全半角の不一致などにより誤判定されている可能性があります。【無償提供部品一覧】シートより型番をコピー＆ペーストにて【部品リスト入力フォーム】にご入力ください。
 |  |  | http://www.p-ban.com/implementation/chip.html
P板.com調達部品(有料） |  |  | P板.com実装サービスで部品調達を希望される場合に○をご選択ください。 ※調達費用のお見積もりは、部品リストの返却と同時にご連絡いたします。 ※ご希望の納期や市場在庫状況によっては、調達が不可となる部品もございますので、予めご了承ください。
パッケージ情報 部品外形/部品仕様 |  |  | 電子部品のパッケージ情報をご入力ください。例：1608 , DIP , 0.5mmピッチQFP , 0.4mmピッチCN
コ メ ン ト |  |  | 特別なご指示のある電子部品について、自由にご入力ください。 例：未実装挿入穴のマスク処理が必要、など
版、変更履歴 |  |  | 部品種毎に、変更履歴を記載してください。 版は、アカウント登録の版に合わせて記載ください。
調達型式、代替型式 |  |  | 無料提供部品の在庫切れや、正確な調達型式を記載いたします。
部品名称見取り表
1.チップ部品（抵抗、コンデンサ）
 |  |  |  |  | 単位：ｍｍ
 |  |  | 電子部品型番 (C:コンデンサ、R:抵抗） | Ａ寸法 | Ｂ寸法
 |  |  | C/R1608 | 1.6 | 0.8
 |  |  | C/R2125 | 2 | 1.25
 |  |  | C/R3216 | 3.2 | 1.6
 |  |  | C/R3225 | 3.2 | 2.5
 |  |  | C/R4532 | 4.5 | 3.2
2.チップタンタルコンデンサ
 |  |  |  |  | 単位：ｍｍ
 |  |  | 電子部品型番 | Ａ寸法 | Ｂ寸法
 |  |  | CT3216 | 3.2 | 1.6
 |  |  | CT3528 | 3.5 | 2.8
 |  |  | CT4726 | 4.7 | 2.6
 |  |  | CT6032 | 6 | 3.2
 |  |  | CT5846 | 5.8 | 4.6
 |  |  | CT7343 | 7.3 | 4.3
3.チップアルミ電解コンデンサ
 |  |  |  |  |  | 単位：ｍｍ
 |  |  | 電子部品型番 | Ａ寸法 | Ｂ寸法 | C寸法
 |  |  | CE33 | 3.3 | 3.3 | φ3.0
 |  |  | CE43 | 4.3 | 4.3 | φ4.0
 |  |  | CE53 | 5.3 | 5.3 | φ5.0
 |  |  | CE66 | 6.6 | 6.6 | φ6.3
 |  |  | CE83 | 8.3 | 8.3 | φ8.0
 |  |  | CE103 | 10.3 | 10.3 | φ10.0
部品取り付け穴は、ピン数に含めてください。
コネクタの場合 |  |  |  |  |  | トランスの場合
部品リストフォーマット変更履歴
2014-02-01 | v2.0 | 松森 | 部品種別の総計を、直接関数に変更
 |  |  | ピン数合計、実装数合計数量を、直接関数に変更
 |  |  | 部品調達見積欄を修正
2014-03-11 | v2.1 | 松森 | *N列、O列が下の方、"○"選択リスト消えていたのを追加
 |  |  | *縮小しても解像度崩れず文字表示するため、フォントを"Meiryo UI"(Windows 標準添付)に変更
 |  |  | *136行目以降を非表示
 |  |  | *"X"列にリストを埋め込み
2014-06-12 | v2.2 | 松森 | *固定行を変更
 |  |  | *在庫状況列に条件付き書式設定
 |  |  | *その他各種バグ修正
2015-03-31 | V2.3 | 松森 | *無償提供部品を記載すると、無償提供部品欄に自動で"○"が表示されるよう条件式を挿入
 |  |  | *併せて、無償提供部品参照用一覧シートの作成・追加
 |  |  | *最小購入数が必要数量を下回る場合、セルを赤色にハッチングする
 |  |  | *シート1の名称変更
 |  |  | *変更履歴シートの追加
2015-06-19 | v2.4 | 松森 | ・ゼロΩ抵抗を無償対象に追加
 |  |  | ・変更履歴の列を追加し、変更履歴シートを削除
 |  |  | ・その他書式、印刷機能の変更
 |  |  | ・無償提供部品の入れ替え
2015-08-14 | v2.5 | 松森 | ・ゼロΩ抵抗の無償対象品が正しく反映されていなかったバグ修正
 |  |  | ・フォームへバージョン情報を埋め込み
2015-11-05 | v2.6 | 上田 | ・無償提供部品(RK73H2ATTD1601F)の抵抗値を正しい値に修正
2015-11-09 | v2.7 | 上田 | ・P板.com調達部品(無料)欄のフォントを変更
2016-01-15 | v2.8 | 箕浦 | ・無償提供部品一覧の「GRM32NF11E106Z」を削除
 |  |  | ・部品リスト入力フォームの4行目F列～L列の計算式が136行目以降を対象としていなかった不具合を修正
2016-01-27 | v2.9 | 箕浦 | ・「無償提供部品一覧」シートの表記修正

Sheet: 部品リスト入力フォーム
Ver.8.0 |  |  | 電 子 部 品 型 番 ※半角英数字 ※サフィックスまで入力必須 | 配 置 記 号 リ フ ァ レ ン ス ※半角英数字） | 個数 | ピ ン 数 (部品取付穴 を含む） |  | 実装/ 未実装 | 部 品 分 類 |  |  | 必要数 実装枚数を入れてください。 ↓ | P板.com 提供 部品 (無料) | P板.com 調達 部品 (有料） | パッケージ情報 部品外形/部品仕様 | コ メ ン ト ※未実装挿入穴の マスク処理が必要、など | 版 変更履歴 | 入荷数 | 返却
No | メーカー | 部品種別 |  |  |  | 1個 あたり | 合計 | 実装個数 | SMD | DIP | 特殊 BGA等 |  |  |  |  |  |  |  |  | 部品調達使用欄
 |  |  |  |  | 21 | 88 | #VALUE! | 21 | 10 | 11 | 0 | 4 | リスト (http://www.p-ban.com/implementation/chip.html)
例 | KOA | チップ抵抗 | RK73B2ATTD1002F | R1,R5,R9,R10 | 4 | 2 | 8 | 未実装 | SMD |  |  |  |  |  | 2012 |  | 4版 型式訂正、個数変更、 実装→未実装へ |  |  | 必要数 | 調達数 | 在庫状況 | 納期
Eg. | Manufacturer | Description | Device | Part no. | Qty. | No. of legs | #VALUE! |  |  |  |  |  |  |  | Package | Remarks |  |  | □
 |  |  |  |  |  |  |  |  |  |  |  |  |  |  |  |  |  |  | □
4 | MURATA | CAPACITOR | GRM155B11A104K | C7 | 1 | 2 | 2 | 実装 | SMD |  |  | 4 | O |  | 1005 | 0.1uF |  |  | □
6 | KOA | RESISTOR | RK73Z1ETTP | R5, R6, R7, R8 | 4 | 2 | 8 | 実装 | SMD |  |  | 16 | O |  | 1005 | 0ohm |  |  | □
10 | Analog Devices Inc. | SENSOR TEMPERATURE | TMP36FSZ | T1 | 1 | 8 | 8 | 実装 | SMD |  |  | 4 |  |  | 8-SOIC |  |  |  | □
11 | HIROSE | CONNECTOR | A3C-50DA-2DSA(71) | C101, C102, C103, C104, C105, C106 | 6 | 50 | 300 | 実装 | DIP |  |  | 24 |  |  | 2x25 header | 2mm pitch, 50 pin |  |  | □
12 | HIROSUGI | Right Angled CONNECTOR | PSR-210154-12 | SP1, SP2, SP3, SP4 | 4 | 12 | 48 | 実装 | DIP |  |  | 16 |  |  | DIP | 2.54mm pitch, 12 pin, 90 degree
13 | HIROSUGI | CONNECTOR | PSS-210204-12 | SP5 | 1 | 12 | 12 | 実装 | DIP |  |  | 4 |  |  | DIP | 2.54mm pitch, 12 pin
14 | MOLEX | CONNECTOR | MOLEX-CONN-2-0554600272 | SW1, SW2, SW3, SW4 | 4 | 2 | 8 | 実装 | SMD |  |  | 16 |  |  | DIP | 2mm, 2POS SMD
15
16
17
18
19
20
21
22
23
24
25
26
27
28
29
30
31
32
33
34
35
36
37
38
39
40
41
42
43
44
45
 |  |  |  |  |  |  |  |  |  |  |  |  |  |  |  |  |  |  | □
 |  |  |  |  |  |  |  |  |  |  |  |  |  |  |  |  |  |  | □
 |  |  |  |  |  |  |  |  |  |  |  |  |  |  |  |  |  |  | □
 |  |  |  |  |  |  |  |  |  |  |  |  |  |  |  |  |  |  | □
 |  |  |  |  |  |  |  |  |  |  |  |  |  |  |  |  |  |  | □
 |  |  |  |  |  |  |  |  |  |  |  |  |  |  |  |  |  |  | □
 |  |  |  |  |  |  |  |  |  |  |  |  |  |  |  |  |  |  | □
 |  |  |  |  |  |  |  |  |  |  |  |  |  |  |  |  |  |  | □
 |  |  |  |  |  |  |  |  |  |  |  |  |  |  |  |  |  |  | □
 |  |  |  |  |  |  |  |  |  |  |  |  |  |  |  |  |  |  | □
 |  |  |  |  |  |  |  |  |  |  |  |  |  |  |  |  |  |  | □
 |  |  |  |  |  |  |  |  |  |  |  |  |  |  |  |  |  |  | □
 |  |  |  |  |  |  |  |  |  |  |  |  |  |  |  |  |  |  | □
 |  |  |  |  |  |  |  |  |  |  |  |  |  |  |  |  |  |  | □
 |  |  |  |  |  |  |  |  |  |  |  |  |  |  |  |  |  |  | □
 |  |  |  |  |  |  |  |  |  |  |  |  |  |  |  |  |  |  | □
 |  |  |  |  |  |  |  |  |  |  |  |  |  |  |  |  |  |  | □
 |  |  |  |  |  |  |  |  |  |  |  |  |  |  |  |  |  |  | □
 |  |  |  |  |  |  |  |  |  |  |  |  |  |  |  |  |  |  | □
 |  |  |  |  |  |  |  |  |  |  |  |  |  |  |  |  |  |  | □
 |  |  |  |  |  |  |  |  |  |  |  |  |  |  |  |  |  |  | □
 |  |  |  |  |  |  |  |  |  |  |  |  |  |  |  |  |  |  | □
 |  |  |  |  |  |  |  |  |  |  |  |  |  |  |  |  |  |  | □
 |  |  |  |  |  |  |  |  |  |  |  |  |  |  |  |  |  |  | □
 |  |  |  |  |  |  |  |  |  |  |  |  |  |  |  |  |  |  | □
 |  |  |  |  |  |  |  |  |  |  |  |  |  |  |  |  |  |  | □
 |  |  |  |  |  |  |  |  |  |  |  |  |  |  |  |  |  |  | □
 |  |  |  |  |  |  |  |  |  |  |  |  |  |  |  |  |  |  | □
 |  |  |  |  |  |  |  |  |  |  |  |  |  |  |  |  |  |  | □
 |  |  |  |  |  |  |  |  |  |  |  |  |  |  |  |  |  |  | □
 |  |  |  |  |  |  |  |  |  |  |  |  |  |  |  |  |  |  | □
 |  |  |  |  |  |  |  |  |  |  |  |  |  |  |  |  |  |  | □
 |  |  |  |  |  |  |  |  |  |  |  |  |  |  |  |  |  |  | □
 |  |  |  |  |  |  |  |  |  |  |  |  |  |  |  |  |  |  | □
 |  |  |  |  |  |  |  |  |  |  |  |  |  |  |  |  |  |  | □
 |  |  |  |  |  |  |  |  |  |  |  |  |  |  |  |  |  |  | □
 |  |  |  |  |  |  |  |  |  |  |  |  |  |  |  |  |  |  | □
 |  |  |  |  |  |  |  |  |  |  |  |  |  |  |  |  |  |  | □
 |  |  |  |  |  |  |  |  |  |  |  |  |  |  |  |  |  |  | □
 |  |  |  |  |  |  |  |  |  |  |  |  |  |  |  |  |  |  | □
 |  |  |  |  |  |  |  |  |  |  |  |  |  |  |  |  |  |  | □
 |  |  |  |  |  |  |  |  |  |  |  |  |  |  |  |  |  |  | □
 |  |  |  |  |  |  |  |  |  |  |  |  |  |  |  |  |  |  | □
 |  |  |  |  |  |  |  |  |  |  |  |  |  |  |  |  |  |  | □
 |  |  |  |  |  |  |  |  |  |  |  |  |  |  |  |  |  |  | □
 |  |  |  |  |  |  |  |  |  |  |  |  |  |  |  |  |  |  | □
 |  |  |  |  |  |  |  |  |  |  |  |  |  |  |  |  |  |  | □

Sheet: 無償提供部品一覧
このシートの内容は変更しないでください。
メーカー型番 |  | メーカー | サイズ | 定数 | 許容差 | 定格
RK73Z1ETTP | ○ | KOA | 1005 | 0 |  | 1A
RK73H1ETTP1R00F | ○ | KOA | 1005 | 1 | ±1% | 0.063W
RK73B1ETTP1R0J | ○ | KOA | 1005 | 1 | ±5% | 0.063W
RK73H1ETTP1R10F | ○ | KOA | 1005 | 1.1 | ±1% | 0.063W
RK73B1ETTP1R1J | ○ | KOA | 1005 | 1.1 | ±5% | 0.063W
RK73H1ETTP1R20F | ○ | KOA | 1005 | 1.2 | ±1% | 0.063W
RK73B1ETTP1R2J | ○ | KOA | 1005 | 1.2 | ±5% | 0.063W
RK73H1ETTP1R30F | ○ | KOA | 1005 | 1.3 | ±1% | 0.063W
RK73B1ETTP1R3J | ○ | KOA | 1005 | 1.3 | ±5% | 0.063W
RK73H1ETTP1R50F | ○ | KOA | 1005 | 1.5 | ±1% | 0.063W
RK73B1ETTP1R5J | ○ | KOA | 1005 | 1.5 | ±5% | 0.063W
RK73H1ETTP1R60F | ○ | KOA | 1005 | 1.6 | ±1% | 0.063W
RK73B1ETTP1R6J | ○ | KOA | 1005 | 1.6 | ±5% | 0.063W
RK73H1ETTP1R80F | ○ | KOA | 1005 | 1.8 | ±1% | 0.063W
RK73B1ETTP1R8J | ○ | KOA | 1005 | 1.8 | ±5% | 0.063W
RK73H1ETTP2R00F | ○ | KOA | 1005 | 2 | ±1% | 0.063W
RK73B1ETTP2R0J | ○ | KOA | 1005 | 2 | ±5% | 0.063W
RK73H1ETTP2R20F | ○ | KOA | 1005 | 2.2 | ±1% | 0.063W
RK73B1ETTP2R2J | ○ | KOA | 1005 | 2.2 | ±5% | 0.063W
RK73H1ETTP2R40F | ○ | KOA | 1005 | 2.4 | ±1% | 0.063W
RK73B1ETTP2R4J | ○ | KOA | 1005 | 2.4 | ±5% | 0.063W
RK73H1ETTP2R70F | ○ | KOA | 1005 | 2.7 | ±1% | 0.063W
RK73B1ETTP2R7J | ○ | KOA | 1005 | 2.7 | ±5% | 0.063W
RK73H1ETTP3R00F | ○ | KOA | 1005 | 3 | ±1% | 0.063W
RK73B1ETTP3R0J | ○ | KOA | 1005 | 3 | ±5% | 0.063W
RK73H1ETTP3R30F | ○ | KOA | 1005 | 3.3 | ±1% | 0.063W
RK73B1ETTP3R3J | ○ | KOA | 1005 | 3.3 | ±5% | 0.063W
RK73H1ETTP3R60F | ○ | KOA | 1005 | 3.6 | ±1% | 0.063W
RK73B1ETTP3R6J | ○ | KOA | 1005 | 3.6 | ±5% | 0.063W
RK73H1ETTP3R90F | ○ | KOA | 1005 | 3.9 | ±1% | 0.063W
RK73B1ETTP3R9J | ○ | KOA | 1005 | 3.9 | ±5% | 0.063W
RK73H1ETTP4R30F | ○ | KOA | 1005 | 4.3 | ±1% | 0.063W
RK73B1ETTP4R3J | ○ | KOA | 1005 | 4.3 | ±5% | 0.063W
RK73H1ETTP4R70F | ○ | KOA | 1005 | 4.7 | ±1% | 0.063W
RK73B1ETTP4R7J | ○ | KOA | 1005 | 4.7 | ±5% | 0.063W
RK73H1ETTP5R10F | ○ | KOA | 1005 | 5.1 | ±1% | 0.063W
RK73B1ETTP5R1J | ○ | KOA | 1005 | 5.1 | ±5% | 0.063W
RK73H1ETTP5R60F | ○ | KOA | 1005 | 5.6 | ±1% | 0.063W
RK73B1ETTP5R6J | ○ | KOA | 1005 | 5.6 | ±5% | 0.063W
RK73H1ETTP6R20F | ○ | KOA | 1005 | 6.2 | ±1% | 0.063W
RK73B1ETTP6R2J | ○ | KOA | 1005 | 6.2 | ±5% | 0.063W
RK73H1ETTP6R80F | ○ | KOA | 1005 | 6.8 | ±1% | 0.063W
RK73B1ETTP6R8J | ○ | KOA | 1005 | 6.8 | ±5% | 0.063W
RK73H1ETTP7R50F | ○ | KOA | 1005 | 7.5 | ±1% | 0.063W
RK73B1ETTP7R5J | ○ | KOA | 1005 | 7.5 | ±5% | 0.063W
RK73H1ETTP8R20F | ○ | KOA | 1005 | 8.2 | ±1% | 0.063W
RK73B1ETTP8R2J | ○ | KOA | 1005 | 8.2 | ±5% | 0.063W
RK73H1ETTP9R10F | ○ | KOA | 1005 | 9.1 | ±1% | 0.063W
RK73B1ETTP9R1J | ○ | KOA | 1005 | 9.1 | ±5% | 0.063W
RK73H1ETTP10R0F | ○ | KOA | 1005 | 10 | ±1% | 0.063W
RK73B1ETTP100J | ○ | KOA | 1005 | 10 | ±5% | 0.063W
RK73H1ETTP11R0F | ○ | KOA | 1005 | 11 | ±1% | 0.063W
RK73B1ETTP110J | ○ | KOA | 1005 | 11 | ±5% | 0.063W
RK73H1ETTP12R0F | ○ | KOA | 1005 | 12 | ±1% | 0.063W
RK73B1ETTP120J | ○ | KOA | 1005 | 12 | ±5% | 0.063W
RK73H1ETTP13R0F | ○ | KOA | 1005 | 13 | ±1% | 0.063W
RK73B1ETTP130J | ○ | KOA | 1005 | 13 | ±5% | 0.063W
RK73H1ETTP15R0F | ○ | KOA | 1005 | 15 | ±1% | 0.063W
RK73B1ETTP150J | ○ | KOA | 1005 | 15 | ±5% | 0.063W
RK73H1ETTP16R0F | ○ | KOA | 1005 | 16 | ±1% | 0.063W
RK73B1ETTP160J | ○ | KOA | 1005 | 16 | ±5% | 0.063W
RK73H1ETTP18R0F | ○ | KOA | 1005 | 18 | ±1% | 0.063W
RK73B1ETTP180J | ○ | KOA | 1005 | 18 | ±5% | 0.063W
RK73H1ETTP20R0F | ○ | KOA | 1005 | 20 | ±1% | 0.063W
RK73B1ETTP200J | ○ | KOA | 1005 | 20 | ±5% | 0.063W
RK73H1ETTP22R0F | ○ | KOA | 1005 | 22 | ±1% | 0.063W
RK73B1ETTP220J | ○ | KOA | 1005 | 22 | ±5% | 0.063W
RK73H1ETTP24R0F | ○ | KOA | 1005 | 24 | ±1% | 0.063W
RK73B1ETTP240J | ○ | KOA | 1005 | 24 | ±5% | 0.063W
RK73H1ETTP27R0F | ○ | KOA | 1005 | 27 | ±1% | 0.063W
RK73B1ETTP270J | ○ | KOA | 1005 | 27 | ±5% | 0.063W
RK73H1ETTP30R0F | ○ | KOA | 1005 | 30 | ±1% | 0.063W
RK73B1ETTP300J | ○ | KOA | 1005 | 30 | ±5% | 0.063W
RK73H1ETTP33R0F | ○ | KOA | 1005 | 33 | ±1% | 0.063W
RK73B1ETTP330J | ○ | KOA | 1005 | 33 | ±5% | 0.063W
RK73H1ETTP36R0F | ○ | KOA | 1005 | 36 | ±1% | 0.063W
RK73B1ETTP360J | ○ | KOA | 1005 | 36 | ±5% | 0.063W
RK73H1ETTP39R0F | ○ | KOA | 1005 | 39 | ±1% | 0.063W
RK73B1ETTP390J | ○ | KOA | 1005 | 39 | ±5% | 0.063W
RK73H1ETTP43R0F | ○ | KOA | 1005 | 43 | ±1% | 0.063W
RK73B1ETTP430J | ○ | KOA | 1005 | 43 | ±5% | 0.063W
RK73H1ETTP47R0F | ○ | KOA | 1005 | 47 | ±1% | 0.063W
RK73B1ETTP470J | ○ | KOA | 1005 | 47 | ±5% | 0.063W
RK73H1ETTP51R0F | ○ | KOA | 1005 | 51 | ±1% | 0.063W
RK73B1ETTP510J | ○ | KOA | 1005 | 51 | ±5% | 0.063W
RK73H1ETTP56R0F | ○ | KOA | 1005 | 56 | ±1% | 0.063W
RK73B1ETTP560J | ○ | KOA | 1005 | 56 | ±5% | 0.063W
RK73H1ETTP62R0F | ○ | KOA | 1005 | 62 | ±1% | 0.063W
RK73B1ETTP620J | ○ | KOA | 1005 | 62 | ±5% | 0.063W
RK73H1ETTP68R0F | ○ | KOA | 1005 | 68 | ±1% | 0.063W
RK73B1ETTP680J | ○ | KOA | 1005 | 68 | ±5% | 0.063W
RK73H1ETTP75R0F | ○ | KOA | 1005 | 75 | ±1% | 0.063W
RK73B1ETTP750J | ○ | KOA | 1005 | 75 | ±5% | 0.063W
RK73H1ETTP82R0F | ○ | KOA | 1005 | 82 | ±1% | 0.063W
RK73B1ETTP820J | ○ | KOA | 1005 | 82 | ±5% | 0.063W
RK73H1ETTP91R0F | ○ | KOA | 1005 | 91 | ±1% | 0.063W
RK73B1ETTP910J | ○ | KOA | 1005 | 91 | ±5% | 0.063W
RK73H1ETTP1000F | ○ | KOA | 1005 | 100 | ±1% | 0.063W
RK73B1ETTP101J | ○ | KOA | 1005 | 100 | ±5% | 0.063W
RK73H1ETTP1100F | ○ | KOA | 1005 | 110 | ±1% | 0.063W
RK73B1ETTP111J | ○ | KOA | 1005 | 110 | ±5% | 0.063W
RK73H1ETTP1200F | ○ | KOA | 1005 | 120 | ±1% | 0.063W
RK73B1ETTP121J | ○ | KOA | 1005 | 120 | ±5% | 0.063W
RK73H1ETTP1300F | ○ | KOA | 1005 | 130 | ±1% | 0.063W
RK73B1ETTP131J | ○ | KOA | 1005 | 130 | ±5% | 0.063W
RK73H1ETTP1500F | ○ | KOA | 1005 | 150 | ±1% | 0.063W
RK73B1ETTP151J | ○ | KOA | 1005 | 150 | ±5% | 0.063W
RK73H1ETTP1600F | ○ | KOA | 1005 | 160 | ±1% | 0.063W
RK73B1ETTP161J | ○ | KOA | 1005 | 160 | ±5% | 0.063W
RK73H1ETTP1800F | ○ | KOA | 1005 | 180 | ±1% | 0.063W
RK73B1ETTP181J | ○ | KOA | 1005 | 180 | ±5% | 0.063W
RK73H1ETTP2000F | ○ | KOA | 1005 | 200 | ±1% | 0.063W
RK73B1ETTP201J | ○ | KOA | 1005 | 200 | ±5% | 0.063W
RK73H1ETTP2200F | ○ | KOA | 1005 | 220 | ±1% | 0.063W
RK73B1ETTP221J | ○ | KOA | 1005 | 220 | ±5% | 0.063W
RK73H1ETTP2400F | ○ | KOA | 1005 | 240 | ±1% | 0.063W
RK73B1ETTP241J | ○ | KOA | 1005 | 240 | ±5% | 0.063W
RK73H1ETTP2700F | ○ | KOA | 1005 | 270 | ±1% | 0.063W
RK73B1ETTP271J | ○ | KOA | 1005 | 270 | ±5% | 0.063W
RK73H1ETTP3000F | ○ | KOA | 1005 | 300 | ±1% | 0.063W
RK73B1ETTP301J | ○ | KOA | 1005 | 300 | ±5% | 0.063W
RK73H1ETTP3300F | ○ | KOA | 1005 | 330 | ±1% | 0.063W
RK73B1ETTP331J | ○ | KOA | 1005 | 330 | ±5% | 0.063W
RK73H1ETTP3600F | ○ | KOA | 1005 | 360 | ±1% | 0.063W
RK73B1ETTP361J | ○ | KOA | 1005 | 360 | ±5% | 0.063W
RK73H1ETTP3900F | ○ | KOA | 1005 | 390 | ±1% | 0.063W
RK73B1ETTP391J | ○ | KOA | 1005 | 390 | ±5% | 0.063W
RK73H1ETTP4300F | ○ | KOA | 1005 | 430 | ±1% | 0.063W
RK73B1ETTP431J | ○ | KOA | 1005 | 430 | ±5% | 0.063W
RK73H1ETTP4700F | ○ | KOA | 1005 | 470 | ±1% | 0.063W
RK73B1ETTP471J | ○ | KOA | 1005 | 470 | ±5% | 0.063W
RK73H1ETTP5100F | ○ | KOA | 1005 | 510 | ±1% | 0.063W
RK73B1ETTP511J | ○ | KOA | 1005 | 510 | ±5% | 0.063W
RK73H1ETTP5600F | ○ | KOA | 1005 | 560 | ±1% | 0.063W
RK73B1ETTP561J | ○ | KOA | 1005 | 560 | ±5% | 0.063W
RK73H1ETTP6200F | ○ | KOA | 1005 | 620 | ±1% | 0.063W
RK73B1ETTP621J | ○ | KOA | 1005 | 620 | ±5% | 0.063W
RK73H1ETTP6800F | ○ | KOA | 1005 | 680 | ±1% | 0.063W
RK73B1ETTP681J | ○ | KOA | 1005 | 680 | ±5% | 0.063W
RK73H1ETTP7500F | ○ | KOA | 1005 | 750 | ±1% | 0.063W
RK73B1ETTP751J | ○ | KOA | 1005 | 750 | ±5% | 0.063W
RK73H1ETTP8200F | ○ | KOA | 1005 | 820 | ±1% | 0.063W
RK73B1ETTP821J | ○ | KOA | 1005 | 820 | ±5% | 0.063W
RK73H1ETTP9100F | ○ | KOA | 1005 | 910 | ±1% | 0.063W
RK73B1ETTP911J | ○ | KOA | 1005 | 910 | ±5% | 0.063W
RK73H1ETTP1001F | ○ | KOA | 1005 | 1.00k | ±1% | 0.063W
RK73B1ETTP102J | ○ | KOA | 1005 | 1k | ±5% | 0.063W
RK73H1ETTP1101F | ○ | KOA | 1005 | 1.10k | ±1% | 0.063W
RK73B1ETTP112J | ○ | KOA | 1005 | 1.1k | ±5% | 0.063W
RK73H1ETTP1201F | ○ | KOA | 1005 | 1.20k | ±1% | 0.063W
RK73B1ETTP122J | ○ | KOA | 1005 | 1.2k | ±5% | 0.063W
RK73H1ETTP1301F | ○ | KOA | 1005 | 1.30k | ±1% | 0.063W
RK73B1ETTP132J | ○ | KOA | 1005 | 1.3k | ±5% | 0.063W
RK73H1ETTP1501F | ○ | KOA | 1005 | 1.50k | ±1% | 0.063W
RK73B1ETTP152J | ○ | KOA | 1005 | 1.5k | ±5% | 0.063W
RK73H1ETTP1601F | ○ | KOA | 1005 | 1.60k | ±1% | 0.063W
RK73B1ETTP162J | ○ | KOA | 1005 | 1.6k | ±5% | 0.063W
RK73H1ETTP1801F | ○ | KOA | 1005 | 1.80k | ±1% | 0.063W
RK73B1ETTP182J | ○ | KOA | 1005 | 1.8k | ±5% | 0.063W
RK73H1ETTP2001F | ○ | KOA | 1005 | 2.00k | ±1% | 0.063W
RK73B1ETTP202J | ○ | KOA | 1005 | 2.0k | ±5% | 0.063W
RK73H1ETTP2201F | ○ | KOA | 1005 | 2.20k | ±1% | 0.063W
RK73B1ETTP222J | ○ | KOA | 1005 | 2.2k | ±5% | 0.063W
RK73H1ETTP2401F | ○ | KOA | 1005 | 2.40k | ±1% | 0.063W
RK73B1ETTP242J | ○ | KOA | 1005 | 2.4k | ±5% | 0.063W
RK73H1ETTP2701F | ○ | KOA | 1005 | 2.70k | ±1% | 0.063W
RK73B1ETTP272J | ○ | KOA | 1005 | 2.7k | ±5% | 0.063W
RK73H1ETTP3001F | ○ | KOA | 1005 | 3.00k | ±1% | 0.063W
RK73B1ETTP302J | ○ | KOA | 1005 | 3.0k | ±5% | 0.063W
RK73H1ETTP3301F | ○ | KOA | 1005 | 3.30k | ±1% | 0.063W
RK73B1ETTP332J | ○ | KOA | 1005 | 3.3k | ±5% | 0.063W
RK73H1ETTP3601F | ○ | KOA | 1005 | 3.60k | ±1% | 0.063W
RK73B1ETTP362J | ○ | KOA | 1005 | 3.6k | ±5% | 0.063W
RK73H1ETTP3901F | ○ | KOA | 1005 | 3.90k | ±1% | 0.063W
RK73B1ETTP392J | ○ | KOA | 1005 | 3.9k | ±5% | 0.063W
RK73H1ETTP4301F | ○ | KOA | 1005 | 4.30k | ±1% | 0.063W
RK73B1ETTP432J | ○ | KOA | 1005 | 4.3k | ±5% | 0.063W
RK73H1ETTP4701F | ○ | KOA | 1005 | 4.70k | ±1% | 0.063W
RK73B1ETTP472J | ○ | KOA | 1005 | 4.7k | ±5% | 0.063W
RK73H1ETTP5101F | ○ | KOA | 1005 | 5.10k | ±1% | 0.063W
RK73B1ETTP512J | ○ | KOA | 1005 | 5.1k | ±5% | 0.063W
RK73H1ETTP5601F | ○ | KOA | 1005 | 5.60k | ±1% | 0.063W
RK73B1ETTP562J | ○ | KOA | 1005 | 5.6k | ±5% | 0.063W
RK73H1ETTP6201F | ○ | KOA | 1005 | 6.20k | ±1% | 0.063W
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

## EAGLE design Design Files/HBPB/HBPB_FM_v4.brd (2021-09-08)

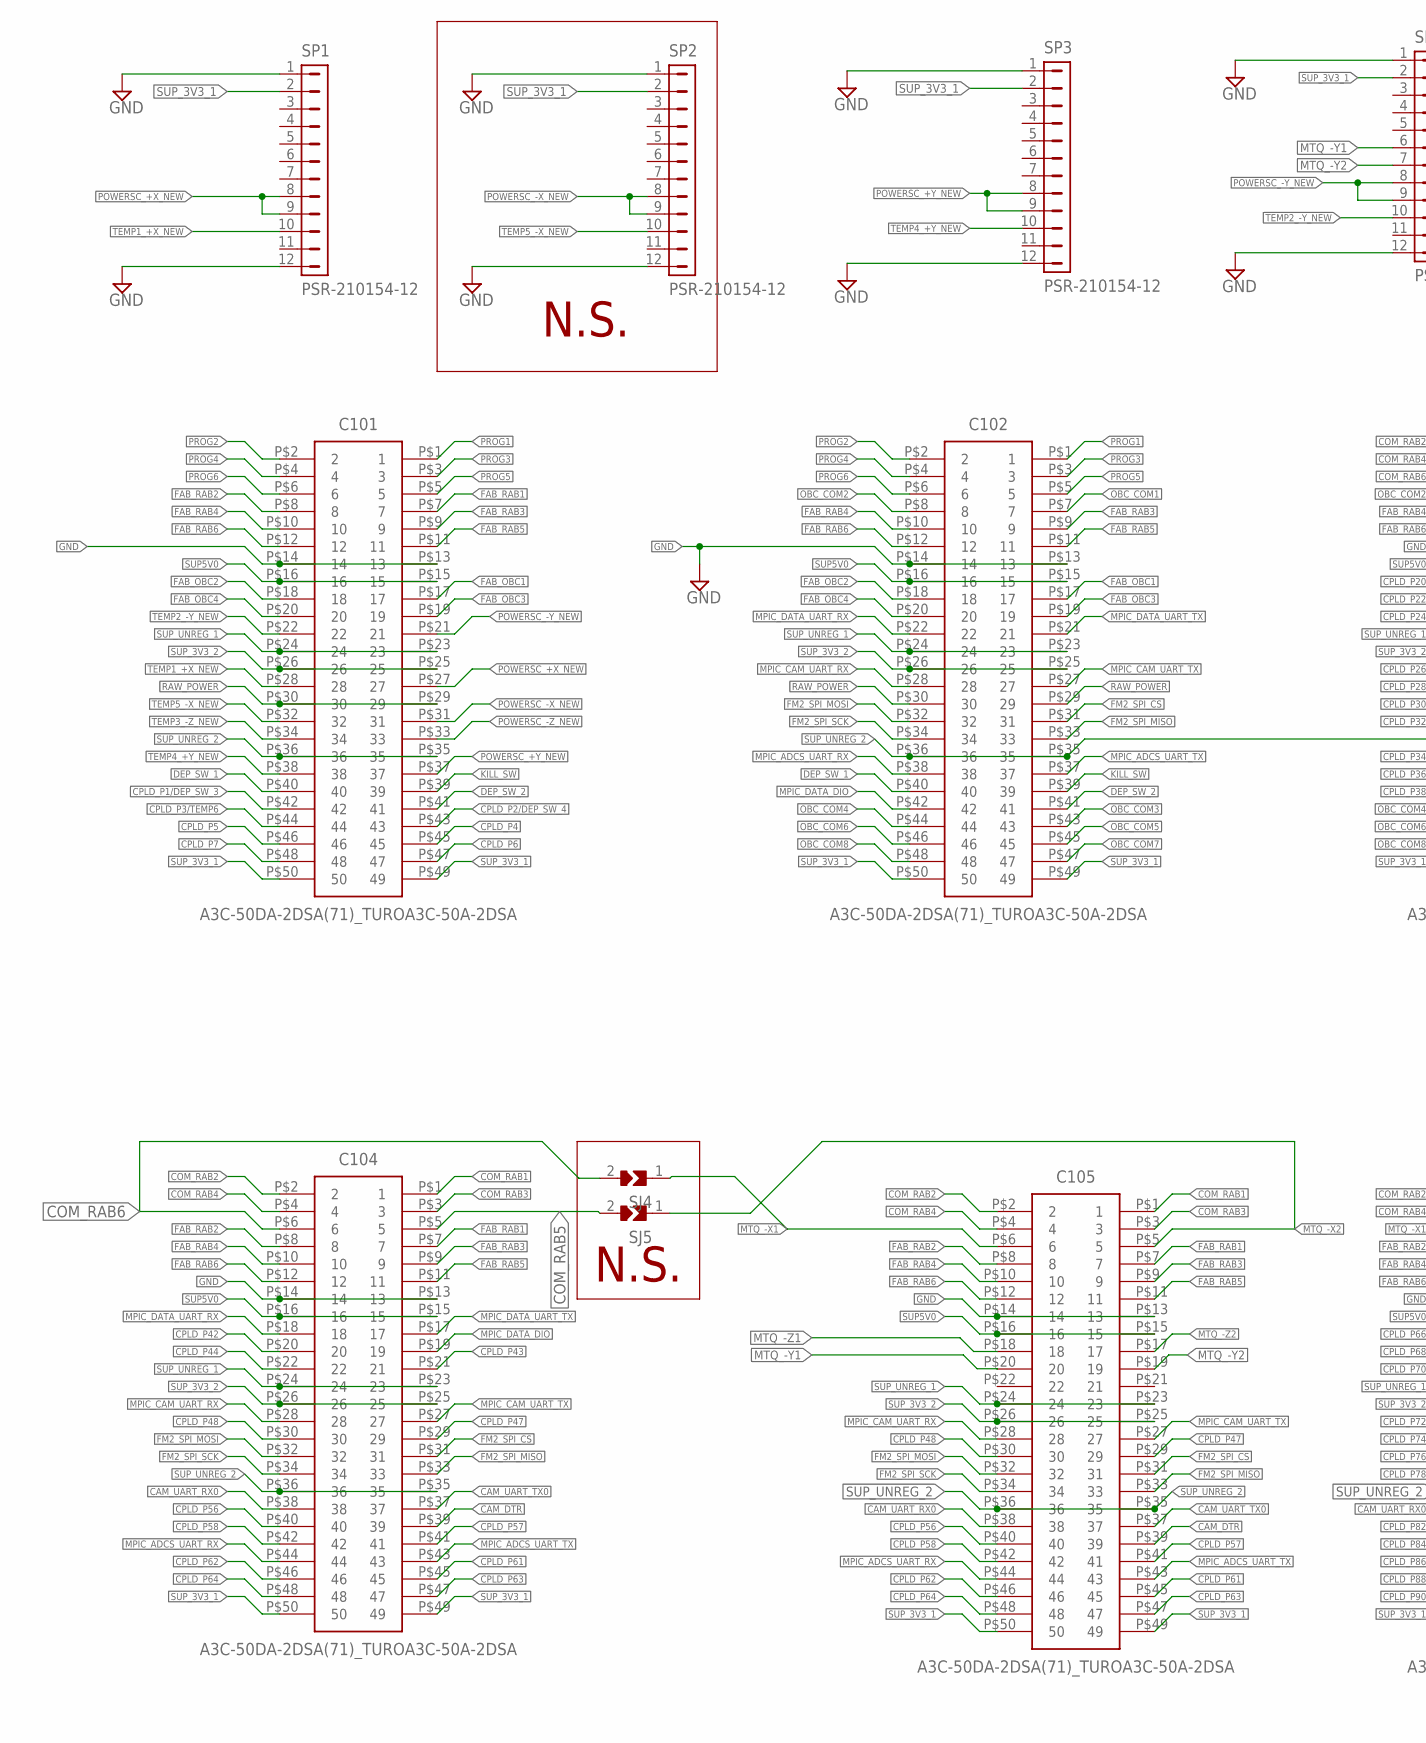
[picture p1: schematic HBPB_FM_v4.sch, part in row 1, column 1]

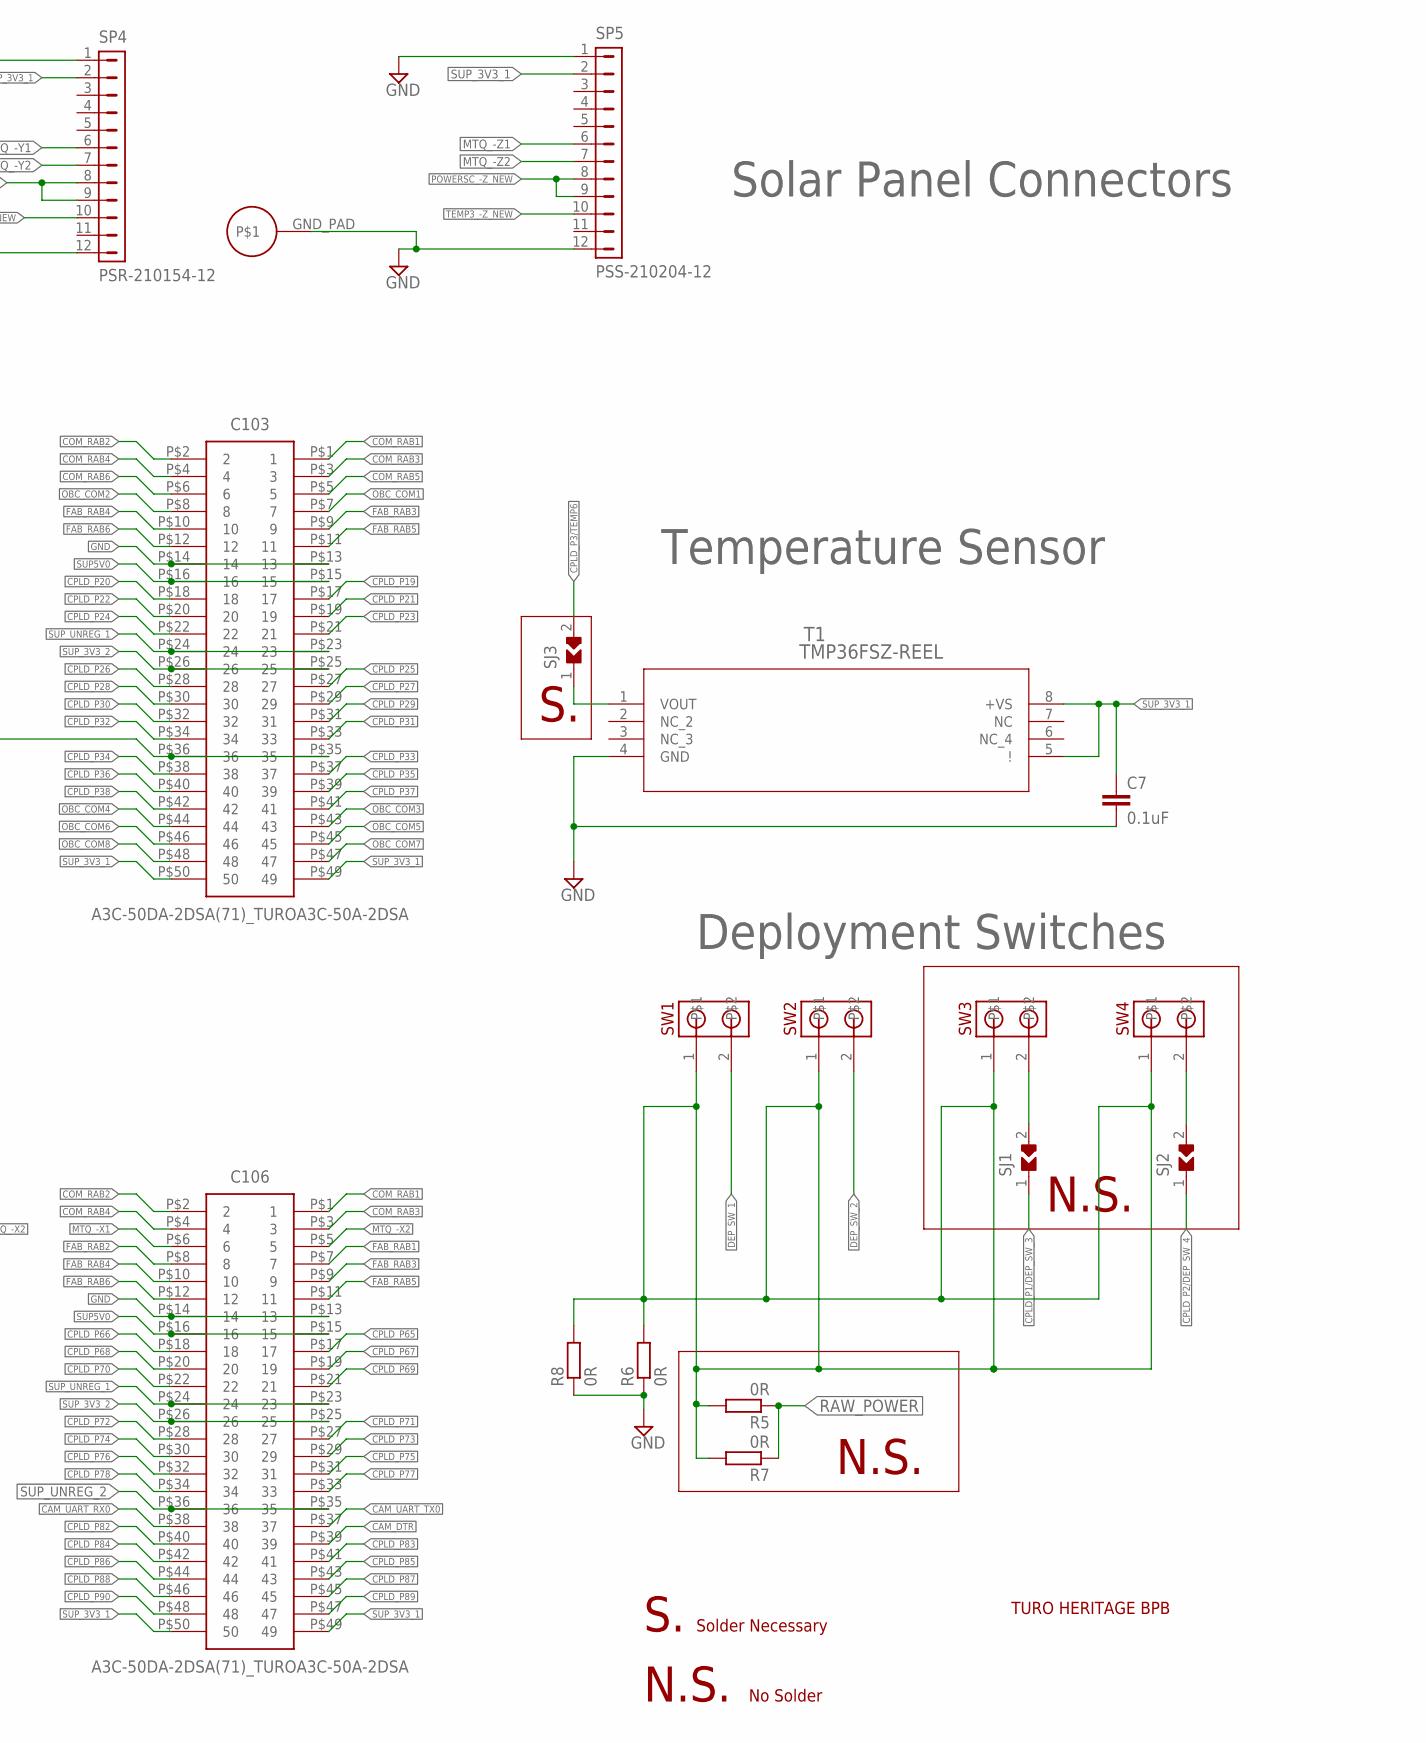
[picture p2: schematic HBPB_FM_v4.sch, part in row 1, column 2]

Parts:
C7: 0.1uF; C0402
C101, C102, C103, C104, C105, C106: A3C-50DA-2DSA(71)_TUROA3C-50A-2DSA; SHDR50W60P200_2X25_5000X400X44_TR
R5, R6, R7, R8: 0R; R3216
SJ1, SJ3, SJ4, SJ5: SJ_BY_TURO; SJ_TURO
SJ2: 0R; SJ_TURO
SP1, SP2, SP3, SP4: PSR-210154-12; PIN1X12/90
SP5: PSS-210204-12; PIN1X12
SW1, SW2, SW3, SW4: MOLEX-CONN-2-0554600272; MOLEX-CONN-2-BIRDS
T1: TMP36FSZ-REEL; R_8
U$1: GND_PAD

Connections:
CAM_DTR: C104.P$39 (39), C105.P$39 (39), C106.P$39 (39)
CAM_UART_RX0: C104.P$38 (38), C105.P$38 (38), C106.P$38 (38)
CAM_UART_TX0: C104.P$37 (37), C105.P$37 (37), C106.P$37 (37)
COM_RAB1: C103.P$1 (1), C104.P$1 (1), C105.P$1 (1), C106.P$1 (1)
COM_RAB2: C103.P$2 (2), C104.P$2 (2), C105.P$2 (2), C106.P$2 (2)
COM_RAB3: C103.P$3 (3), C104.P$3 (3), C105.P$3 (3), C106.P$3 (3)
COM_RAB4: C103.P$4 (4), C104.P$4 (4), C105.P$4 (4), C106.P$4 (4)
COM_RAB5: C103.P$5 (5), C104.P$5 (5), SJ5.2
COM_RAB6: C103.P$6 (6), C104.P$6 (6), SJ4.2
CPLD_P1/DEP_SW_3: C101.P$42 (42), SJ1.1
CPLD_P2/DEP_SW_4: C101.P$43 (43), SJ2.1
CPLD_P3/TEMP6: C101.P$44 (44), SJ3.2
CPLD_P4: C101.P$45 (45)
CPLD_P5: C101.P$46 (46)
CPLD_P6: C101.P$47 (47)
CPLD_P7: C101.P$48 (48)
CPLD_P19: C103.P$17 (17)
CPLD_P20: C103.P$18 (18)
CPLD_P21: C103.P$19 (19)
CPLD_P22: C103.P$20 (20)
CPLD_P23: C103.P$21 (21)
CPLD_P24: C103.P$22 (22)
CPLD_P25: C103.P$27 (27)
CPLD_P26: C103.P$28 (28)
CPLD_P27: C103.P$29 (29)
CPLD_P28: C103.P$30 (30)
CPLD_P29: C103.P$31 (31)
CPLD_P30: C103.P$32 (32)
CPLD_P31: C103.P$33 (33)
CPLD_P32: C103.P$34 (34)
CPLD_P33: C103.P$37 (37)
CPLD_P34: C103.P$38 (38)
CPLD_P35: C103.P$39 (39)
CPLD_P36: C103.P$40 (40)
CPLD_P37: C103.P$41 (41)
CPLD_P38: C103.P$42 (42)
CPLD_P42: C104.P$20 (20)
CPLD_P43: C104.P$21 (21)
CPLD_P44: C104.P$22 (22)
CPLD_P47: C104.P$29 (29), C105.P$29 (29)
CPLD_P48: C104.P$30 (30), C105.P$30 (30)
CPLD_P56: C104.P$40 (40), C105.P$40 (40)
CPLD_P57: C104.P$41 (41), C105.P$41 (41)
CPLD_P58: C104.P$42 (42), C105.P$42 (42)
CPLD_P61: C104.P$45 (45), C105.P$45 (45)
CPLD_P62: C104.P$46 (46), C105.P$46 (46)
CPLD_P63: C104.P$47 (47), C105.P$47 (47)
CPLD_P64: C104.P$48 (48), C105.P$48 (48)
CPLD_P65: C106.P$17 (17)
CPLD_P66: C106.P$18 (18)
CPLD_P67: C106.P$19 (19)
CPLD_P68: C106.P$20 (20)
CPLD_P69: C106.P$21 (21)
CPLD_P70: C106.P$22 (22)
CPLD_P71: C106.P$27 (27)
CPLD_P72: C106.P$28 (28)
CPLD_P73: C106.P$29 (29)
CPLD_P74: C106.P$30 (30)
CPLD_P75: C106.P$31 (31)
CPLD_P76: C106.P$32 (32)
CPLD_P77: C106.P$33 (33)
CPLD_P78: C106.P$34 (34)
CPLD_P82: C106.P$40 (40)
CPLD_P83: C106.P$41 (41)
CPLD_P84: C106.P$42 (42)
CPLD_P85: C106.P$43 (43)
CPLD_P86: C106.P$44 (44)
CPLD_P87: C106.P$45 (45)
CPLD_P88: C106.P$46 (46)
CPLD_P89: C106.P$47 (47)
CPLD_P90: C106.P$48 (48)
DEP_SW_1: C101.P$40 (40), C102.P$40 (40), SW1.2
DEP_SW_2: C101.P$41 (41), C102.P$41 (41), SW2.2
DEP_SW_POWER: R5.2, R6.2, R7.2, R8.2, SW1.1, SW2.1, SW3.1, SW4.1
FAB_OBC1: C101.P$17 (17), C102.P$17 (17)
FAB_OBC2: C101.P$18 (18), C102.P$18 (18)
FAB_OBC3: C101.P$19 (19), C102.P$19 (19)
FAB_OBC4: C101.P$20 (20), C102.P$20 (20)
FAB_RAB1: C101.P$7 (7), C104.P$7 (7), C105.P$7 (7), C106.P$7 (7)
FAB_RAB2: C101.P$8 (8), C104.P$8 (8), C105.P$8 (8), C106.P$8 (8)
FAB_RAB3: C101.P$9 (9), C102.P$9 (9), C103.P$9 (9), C104.P$9 (9), C105.P$9 (9), C106.P$9 (9)
FAB_RAB4: C101.P$10 (10), C102.P$10 (10), C103.P$10 (10), C104.P$10 (10), C105.P$10 (10), C106.P$10 (10)
FAB_RAB5: C101.P$11 (11), C102.P$11 (11), C103.P$11 (11), C104.P$11 (11), C105.P$11 (11), C106.P$11 (11)
FAB_RAB6: C101.P$12 (12), C102.P$12 (12), C103.P$12 (12), C104.P$12 (12), C105.P$12 (12), C106.P$12 (12)
FM2_SPI_CS: C102.P$31 (31), C104.P$31 (31), C105.P$31 (31)
FM2_SPI_MISO: C102.P$33 (33), C104.P$33 (33), C105.P$33 (33)
FM2_SPI_MOSI: C102.P$32 (32), C104.P$32 (32), C105.P$32 (32)
FM2_SPI_SCK: C102.P$34 (34), C104.P$34 (34), C105.P$34 (34)
GND: C7.2, C101.P$13 (13), C101.P$14 (14), C102.P$13 (13), C102.P$14 (14), C103.P$13 (13), C103.P$14 (14), C104.P$13 (13), C104.P$14 (14), C105.P$13 (13), C105.P$14 (14), C106.P$13 (13), C106.P$14 (14), R6.1, R8.1, SP1.1, SP1.12, SP2.1, SP2.12, SP3.1, SP3.12, SP4.1, SP4.12, SP5.1, SP5.12, T1.4 (GND), U$1.GND_PAD
KILL_SW: C101.P$39 (39), C102.P$39 (39)
MPIC_ADCS_UART_RX: C102.P$38 (38), C104.P$44 (44), C105.P$44 (44)
MPIC_ADCS_UART_TX: C102.P$37 (37), C104.P$43 (43), C105.P$43 (43)
MPIC_CAM_UART_RX: C102.P$28 (28), C104.P$28 (28), C105.P$28 (28)
MPIC_CAM_UART_TX: C102.P$27 (27), C104.P$27 (27), C105.P$27 (27)
MPIC_DATA_DIO: C102.P$42 (42), C104.P$19 (19)
MPIC_DATA_UART_RX: C102.P$22 (22), C104.P$18 (18)
MPIC_DATA_UART_TX: C102.P$21 (21), C104.P$17 (17)
MTQ_-X1: C105.P$6 (6), C106.P$6 (6), SJ4.1
MTQ_-X2: C105.P$5 (5), C106.P$5 (5), SJ5.1
MTQ_-Y1: C105.P$20 (20), SP4.6
MTQ_-Y2: C105.P$19 (19), SP4.7
MTQ_-Z1: C105.P$18 (18), SP5.6
MTQ_-Z2: C105.P$17 (17), SP5.7
unnamed: SJ2.2, SW4.2
unnamed: SJ1.2, SW3.2
unnamed: SJ3.1, T1.1 (VOUT)
OBC_COM1: C102.P$7 (7), C103.P$7 (7)
OBC_COM2: C102.P$8 (8), C103.P$8 (8)
OBC_COM3: C102.P$43 (43), C103.P$43 (43)
OBC_COM4: C102.P$44 (44), C103.P$44 (44)
OBC_COM5: C102.P$45 (45), C103.P$45 (45)
OBC_COM6: C102.P$46 (46), C103.P$46 (46)
OBC_COM7: C102.P$47 (47), C103.P$47 (47)
OBC_COM8: C102.P$48 (48), C103.P$48 (48)
POWERSC_+X_NEW: C101.P$27 (27), SP1.8, SP1.9
POWERSC_+Y_NEW: C101.P$37 (37), SP3.8, SP3.9
POWERSC_-X_NEW: C101.P$31 (31), SP2.8, SP2.9
POWERSC_-Y_NEW: C101.P$21 (21), SP4.8, SP4.9
POWERSC_-Z_NEW: C101.P$33 (33), SP5.8, SP5.9
PROG1: C101.P$1 (1), C102.P$1 (1)
PROG2: C101.P$2 (2), C102.P$2 (2)
PROG3: C101.P$3 (3), C102.P$3 (3)
PROG4: C101.P$4 (4), C102.P$4 (4)
PROG5: C101.P$5 (5), C102.P$5 (5)
PROG6: C101.P$6 (6), C102.P$6 (6)
RAW_POWER: C101.P$29 (29), C101.P$30 (30), C102.P$29 (29), C102.P$30 (30), R5.1, R7.1
SUP5V0: C101.P$15 (15), C101.P$16 (16), C102.P$15 (15), C102.P$16 (16), C103.P$15 (15), C103.P$16 (16), C104.P$15 (15), C104.P$16 (16), C105.P$15 (15), C105.P$16 (16), C106.P$15 (15), C106.P$16 (16)
SUP_3V3_1: C7.1, C101.P$49 (49), C101.P$50 (50), C102.P$49 (49), C102.P$50 (50), C103.P$49 (49), C103.P$50 (50), C104.P$49 (49), C104.P$50 (50), C105.P$49 (49), C105.P$50 (50), C106.P$49 (49), C106.P$50 (50), SP1.2, SP2.2, SP3.2, SP4.2, SP5.2, T1.5 (!), T1.8 (+VS)
SUP_3V3_2: C101.P$25 (25), C101.P$26 (26), C102.P$25 (25), C102.P$26 (26), C103.P$25 (25), C103.P$26 (26), C104.P$25 (25), C104.P$26 (26), C105.P$25 (25), C105.P$26 (26), C106.P$25 (25), C106.P$26 (26)
SUP_UNREG_1: C101.P$23 (23), C101.P$24 (24), C102.P$23 (23), C102.P$24 (24), C103.P$23 (23), C103.P$24 (24), C104.P$23 (23), C104.P$24 (24), C105.P$23 (23), C105.P$24 (24), C106.P$23 (23), C106.P$24 (24)
SUP_UNREG_2: C101.P$35 (35), C101.P$36 (36), C102.P$35 (35), C102.P$36 (36), C103.P$35 (35), C103.P$36 (36), C104.P$35 (35), C104.P$36 (36), C105.P$35 (35), C105.P$36 (36), C106.P$35 (35), C106.P$36 (36)
TEMP1_+X_NEW: C101.P$28 (28), SP1.10
TEMP2_-Y_NEW: C101.P$22 (22), SP4.10
TEMP3_-Z_NEW: C101.P$34 (34), SP5.10
TEMP4_+Y_NEW: C101.P$38 (38), SP3.10
TEMP5_-X_NEW: C101.P$32 (32), SP2.10

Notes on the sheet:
Temperature Sensor
Deployment Switches
Solar Panel Connectors
TURO HERITAGE BPB
N.S.
Solder Necessary
No Solder

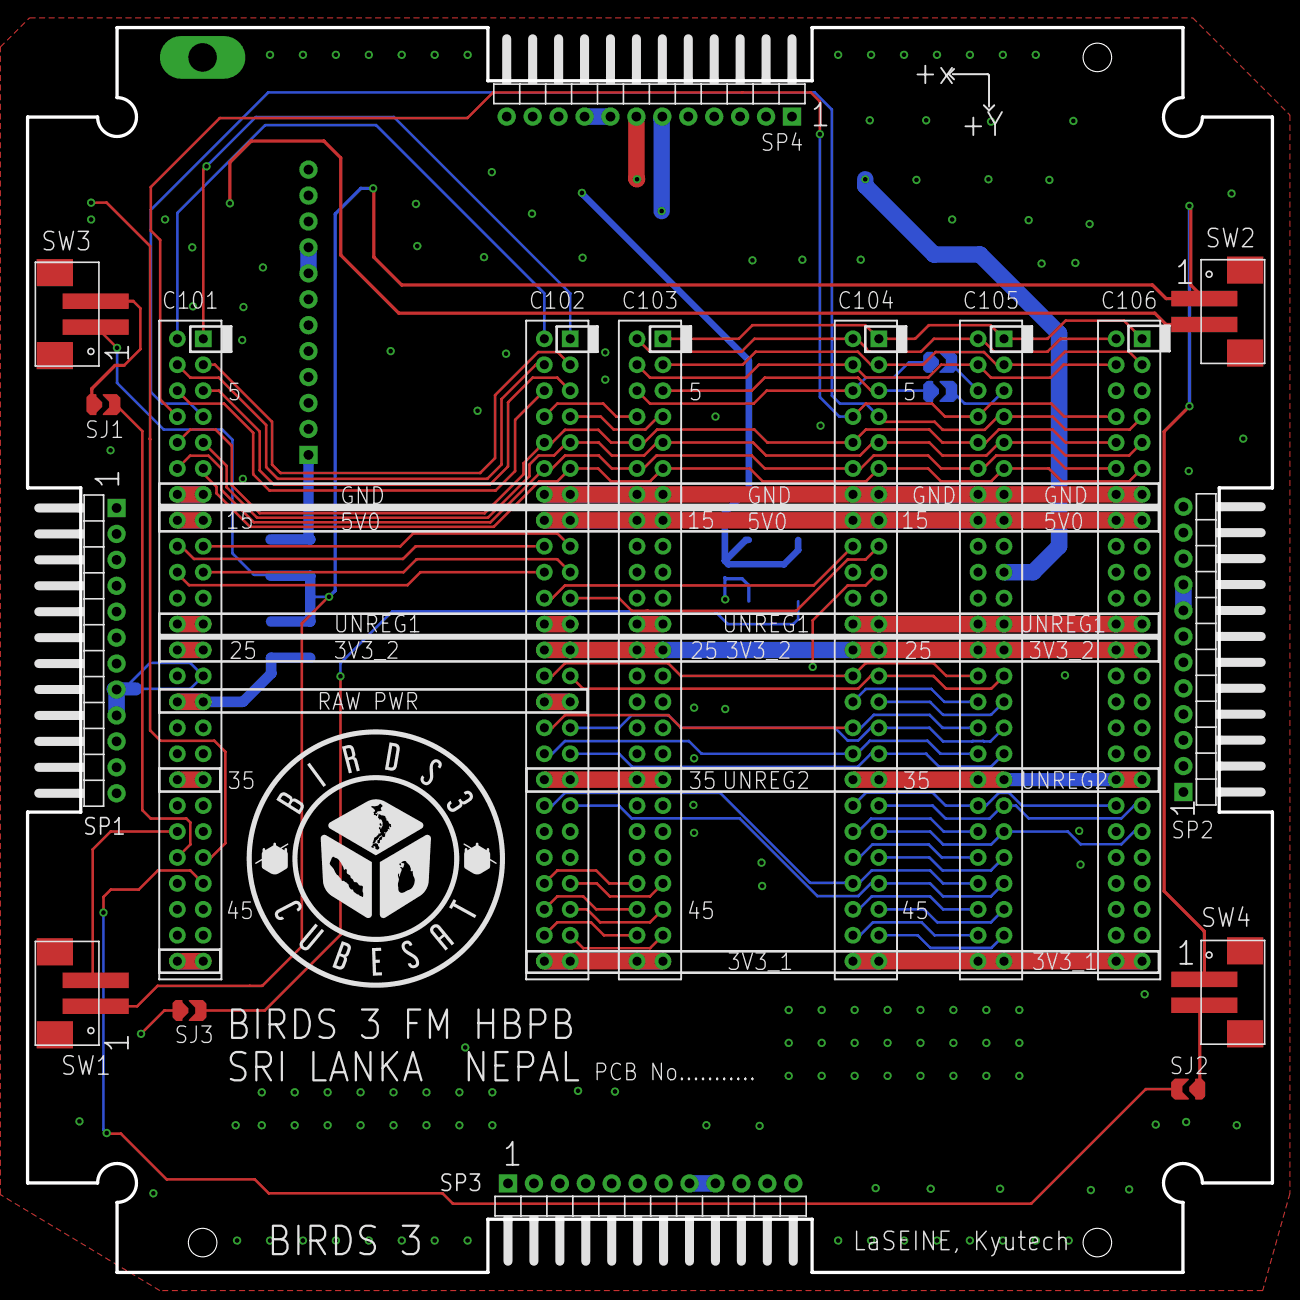
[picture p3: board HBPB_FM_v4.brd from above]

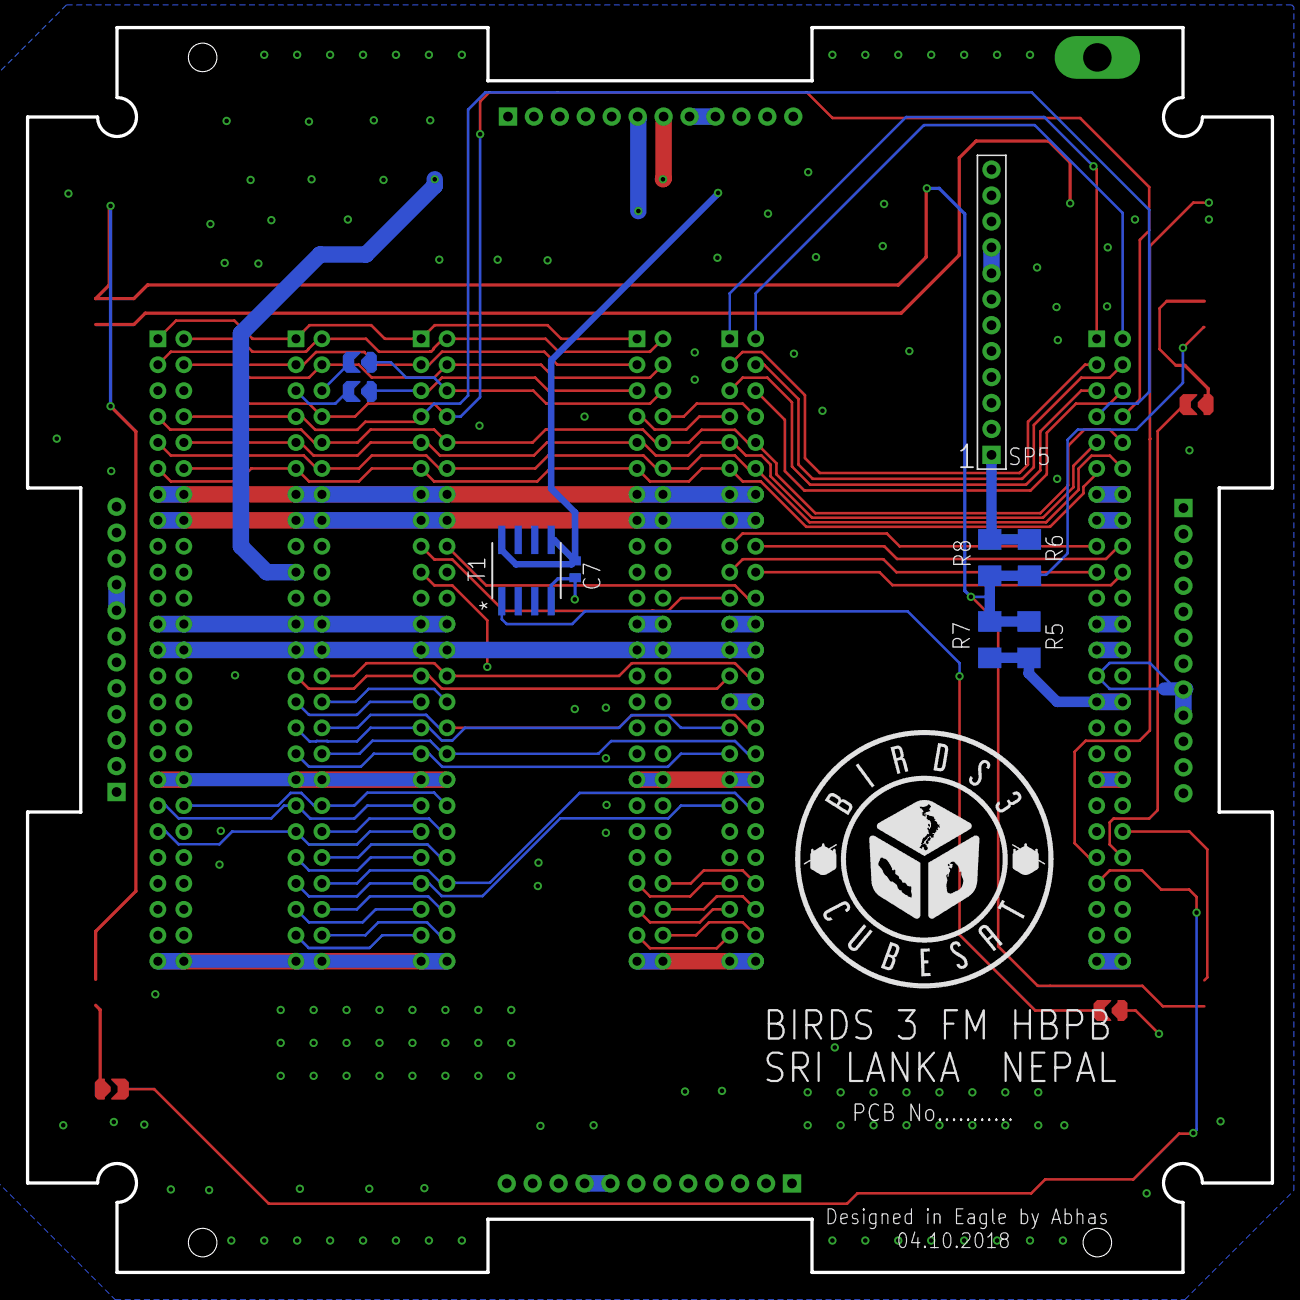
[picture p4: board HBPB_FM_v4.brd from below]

Board: 6 copper layers, 96.0 x 96.0 mm, 27 parts (9 on the bottom side), 86 nets.
